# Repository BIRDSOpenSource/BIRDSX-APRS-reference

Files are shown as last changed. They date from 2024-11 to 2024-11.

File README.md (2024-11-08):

<div align="center">
  <a href="https://lean-sat.org/opensource/">
  
  </a>
</div> 

<div align="center">
  birds x
</div>

# BIRDSX-APRS-reference
 Documentation for the APRS Reference files of the BIRDSX Satellite.

## About the BIRDSX Program:

The Mission Statement of the Project is:

> “The goal of our project is to bring diversity to the space sector and democratize the usage of space.”

The project is led by Kyushu Institute of Technology in Japan and involves students from XXX,XXX and Japan.

Satellite Names: Dragonfly (Japan), 

Stakeholders:  Our stakeholders are Kyushu Institute of Technology (Kyutech) and the Association for Radio Digital Communications (ARDC).

Project duration: 2023-2024

CubeSat: 2U (20x10x10) cm3

Weight: 1.13kg

Launch Date: 21st February 2025

BIRDS-X project is a 2U CubeSat dedicated to amateur radio communication.

## Organisation structure

```bash

├── .gitattributes
├── BIRDS_Solar-panel-attachment-procedure_v2.2.pdf
├── Manual (SML-2K1MV1) (1).pdf
├── LICENSE
└── README.md

```

## Features

## I like this project, can I help you?
You are welcome 🙂

* Give us a star ⭐
* Watch repository to be notified about updates 👀
* If you will find some errors, report them in Issues 🐞
* Try Birds designs on some real computer and let us know how it worked in Discussions. 💬
* We would greatly appreciate if you would also tell others about this ecosystem, it helps us to improve BIRDS Open Source. Thank you!

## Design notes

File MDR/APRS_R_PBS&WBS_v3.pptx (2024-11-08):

## APRS Reference Board (APRS-R)

## Function and Performance

- Purpose : Provide satellite APRS digipeating for Amateur Radio Community.
- Function 1: Digipeater APRS packets from amateur radio stations on the ground.
Performance 1a: Transmit satellite APRS beacon to ground
Performance 1b: Receive and retransmit APRS packets from amateur radio stations.
Performance 1c: Transfer the received data packets to desired micro controller.

## Function and Performace

- Function 2 : Store the received data.
Performance 2a: Store the data to satellite’s specified memory location.
- Function 3 : Send data to the main ground stations.
Performance 3a: Transfer stored data to COMM MCU for download via UHF 4800 bps to ground stations.

## PBS

Satellite
1.1
Payload
1.1.2
APRS Reference
1.1.2.1
Transceiver
1.1.2.1.1
Terminal Node Controller (TNC)
1.1.2.1.2
Main Control Unit (MCU)
1.1.2.1.3
Memory
1.1.2.1.4
VHF Antenna
1.1.2.1.5

## WBS

Payload
1.1.2
APRS Reference
1.1.2.1
Transceiver
1.1.2.1.1
Terminal Node Controller (TNC)
1.1.2.1.2
Procurement
1.1.2.1.1.1
Assemble
1.1.2.1.1.2
Test
1.1.2.1.1.3
Procurement
1.1.2.1.2.1
Assemble
1.1.2.1.2.2
Test
1.1.2.1.2.3

## WBS (cont’l)

Payload
1.1.2
APRS Reference
1.1.2.1
Main Control Unit (MCU)
1.1.2.1.3
Memory
1.1.2.1.4
Procurement
1.1.2.1.3.1
Assemble
1.1.2.1.3.2
Test
1.1.2.1.3.3
Procurement
1.1.2.1.4.1
Assemble
1.1.2.1.4.2
Test
1.1.2.1.4.3

## WBS (cont’l)

Payload
1.1.2
APRS Reference
1.1.2.1
Main Control Unit (MCU)
1.1.2.1.3
Memory
1.1.2.1.4
Procurement
1.1.2.1.3.1
Assemble
1.1.2.1.3.2
Test
1.1.2.1.3.3
Procurement
1.1.2.1.4.1
Assemble
1.1.2.1.4.2
Test
1.1.2.1.4.3

## WBS (cont’l)

Payload
1.1.2
APRS Reference
1.1.2.1
VHF Antenna
1.1.2.1.5
Procurement
1.1.2.1.3.1
Assemble
1.1.2.1.3.2
Test
1.1.2.1.3.3

## Block Diagram

APRS Reference Payload

ARPS Reference MCU

VHF band

UART

TNC/APRS module

1200bps
AFSK

VHF FM Transceiver

Mission Boss

OBC

SPI

Flash Memory

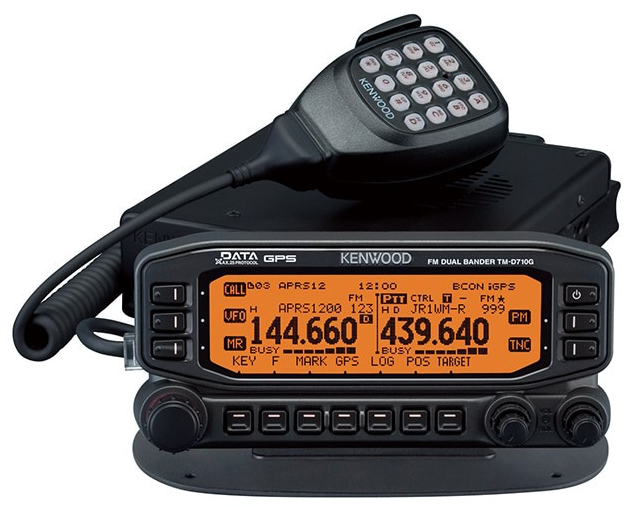
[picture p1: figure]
TM-D710G/TM-D710GS（生産完了品） | FMトランシーバー | アマチュア無線 | 無線通信 | KENWOOD

Amateur Radio Users or
Ground Terminal

UHF band

COMM MCU

COMM TRX

Ground station

9

## Link Budget

ELEVATION | | 10° | 20° | 30° | 40° | 50° | 60° | 70° | 80°
GROUND STATION
Transmit Output Power | [W] | 50 | 50 | 50 | 50 | 50 | 50 | 50 | 50
Transmit Output Power | [dBm] | 47 | 47 | 47 | 47 | 47 | 47 | 47 | 47
Antenna Gain | [dB] | 16 | 16 | 16 | 16 | 16 | 16 | 16 | 16
Transmission Line Loss | [dB] | 3.5 | 3.5 | 3.5 | 3.5 | 3.5 | 3.5 | 3.5 | 3.5
EIRP | [dBm] | 59.5 | 59.5 | 59.5 | 59.5 | 59.5 | 59.5 | 59.5 | 59.5
UPLINK PATH
GS Antenna Pointing Loss | [dB] | 3 | 3 | 3 | 3 | 3 | 3 | 3 | 3
Polarization Loss | [dB] | 3 | 3 | 3 | 3 | 3 | 3 | 3 | 3
Atmospheric + Ionospheric Losses | [dB] | 1.4 | 1.4 | 1.4 | 1.4 | 1.4 | 1.4 | 1.4 | 1.4
Path Loss | [dB] | 139.2 | 135.9 | 133.5 | 130.9 | 130.3 | 129.4 | 128.7 | 128.3
Antenna Pointing Loss | [dB] | 3 | 3 | 3 | 3 | 3 | 3 | 3 | 3
Effective Attenuation | [dB] | 137.1 | 133.8 | 131.4 | 128.8 | 128.2 | 127.3 | 126.6 | 126.2
Power at the satellite | [dBm] | -90.1 | -86.8 | -84.4 | -81.8 | -81.2 | -80.3 | -79.6 | -79.2
SATELLITE
Antenna Gain + Cable Loss | [dB] | 0.4 | 0.4 | 0.4 | 0.4 | 0.4 | 0.4 | 0.4 | 0.4
Transceiver Received Power | [dBm] | -89.7 | -86.4 | -84 | -81.4 | -80.8 | -79.9 | -79.2 | -78.8
Minimum Received Power | [dBm] | -85 | -85 | -85 | -85 | -85 | -85 | -85 | -85
Link Margin | [dB] | -4.7 | -1.4 | 1 | 3.6 | 4.2 | 5.1 | 5.8 | 6.2

## Link Budget

ELEVATION | | 10° | 20° | 30° | 40° | 50° | 60° | 70° | 80°
SATELLITE
Transmit Output Power | [W] | 0.48 | 0.48 | 0.48 | 0.48 | 0.48 | 0.48 | 0.48 | 0.48
Transmit Output Power | [dBm] | 27.8 | 27.8 | 27.8 | 27.8 | 27.8 | 27.8 | 27.8 | 27.8
Antenna Gain + Cable Loss | [dB] | 0.4 | 0.4 | 0.4 | 0.4 | 0.4 | 0.4 | 0.4 | 0.4
EIRP | [dBm] | 28.2 | 28.2 | 28.2 | 28.2 | 28.2 | 28.2 | 28.2 | 28.2
DOWNLINK PATH
Satellite Antenna Pointing Loss | [dB] | 3 | 3 | 3 | 3 | 3 | 3 | 3 | 3
Polarization Loss | [dB] | 3 | 3 | 3 | 3 | 3 | 3 | 3 | 3
Atmospheric + Ionospheric Losses | [dB] | 1.4 | 1.4 | 1.4 | 1.4 | 1.4 | 1.4 | 1.4 | 1.4
Path Loss | [dB] | 139.2 | 135.9 | 133.5 | 130.9 | 130.3 | 129.4 | 128.7 | 128.3
Antenna Pointing Loss | [dB] | 3 | 3 | 3 | 3 | 3 | 3 | 3 | 3
Effective Attenuation | [dB] | 149.2 | 145.9 | 143.5 | 140.9 | 140.3 | 139.4 | 138.7 | 138.3
Power at the ground station | [dBm] | -121.4 | -118.1 | -115.7 | -113.1 | -112.5 | -111.6 | -110.9 | -110.5
GROUND STATION
Antenna Gain | [dB] | 16 | 16 | 16 | 16 | 16 | 16 | 16 | 16
Transmission Line Loss | [dB] | 3.5 | 3.5 | 3.5 | 3.5 | 3.5 | 3.5 | 3.5 | 3.5
Transceiver Received Power | [dBm] | -108.9 | -105.6 | -103.2 | -100.6 | -100 | -99.1 | -98.4 | -98
Minimum Received Power | [dBm] | -110 | -110 | -110 | -110 | -110 | -110 | -110 | -110
Link Margin | [dB] | 1.1 | 4.4 | 6.8 | 9.4 | 10 | 10.9 | 11.6 | 12

## RAS

SR 1.1 – payload shall be controllable through an uplink command from a control ground station.
Design Requirements | Verification Requirements | Verification Method
Command will be sent from ground station using UHF uplink frequency | Measure receivable signal power of COMM transceiver | Using spectrum analyzer
OBC will relay the command to Mission Boss to activate APRS Reference payload | Check if the APRS/SF-WARD payload is activated/deactivated | Using terminal software to read APRS Reference MCU

## RAS

SR 1.2 – VHF transceiver operating in half-duplex will receive data from amateur radio users/ground terminal.
Design Requirements | Verification Requirements | Verification Method
Receiver will demodulate FM signal received | Check AFSK output of Receiver | Using spectrum analyzer
TNC will decode received AFSK signal | Check data output of TNC | Display Serial Output of TNC through Serial Monitor on PC
APRS Reference payload will receive transmitted data and store it. | Check received data if it matches transmitted data through wired testing | Display received OBC data through Serial on PC
| Check stored data in flash memory. | Read Flash Memory through APRS Reference Serial Interface

SR 1.2 – VHF transceiver operating in half-duplex will receive mission data from ground sensors.

## RAS

SR 1.3 – Payload shall store received packets (APRS message and ground sensor) into memory
Design Requirements | Verification Requirements | Verification Method
APRS Reference MCU shall process received AX.25 frame into correct fields | Check processed data of APRS Reference MCU | Display processed data through serial interface
Flash memory capacity of at least 32MB | Check specification and writable memory | Through write operations

SR 1.2 – VHF transceiver operating in half-duplex will receive mission data from ground sensors.

## RAS

SR 1.4 – Payload shall transmit stored data to ground station upon command from ground station using COM data downlink frequency
Design Requirements | Verification Requirements | Verification Method
COMM MCU shall read stored memory in APRS Reference Flash memory for downlink | Check data transmitted by COMM | Display received data

SR 1.2 – VHF transceiver operating in half-duplex will receive mission data from ground sensors.

## Schedule

TASK | 2022 | | | | 2023 | | | | | | | | | | | | | | | | | | | | | | | | | | | | | | | | | | | | | | | | | | | | | | | | 2024
| Dec | | | | Jan | | | | Feb | | | | Mar | | | | Apr | | | | May | | | | Jun | | | | Jul | | | | Aug | | | | Sep | | | | Oct | | | | Nov | | | | Dec | | | | Jan | | | | Feb
| 1 | 2 | 3 | 4 | 1 | 2 | 3 | 4 | 1 | 2 | 3 | 4 | 1 | 2 | 3 | 4 | 1 | 2 | 3 | 4 | 1 | 2 | 3 | 4 | 1 | 2 | 3 | 4 | 1 | 2 | 3 | 4 | 1 | 2 | 3 | 4 | 1 | 2 | 3 | 4 | 1 | 2 | 3 | 4 | 1 | 2 | 3 | 4 | 1 | 2 | 3 | 4 | 1 | 2 | 3 | 4 | 1 | 2 | 3 | 4
Check legacy missions' info
Procurement Components
Bread board model
Programming MCU
EM development
Integration with other satellite subsystems
Space Environment Test
FM development and final space environment tests

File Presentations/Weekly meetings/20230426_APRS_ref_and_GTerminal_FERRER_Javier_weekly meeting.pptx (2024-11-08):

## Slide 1

APRS Reference & Ground Terminal – Weekly meeting

FERRER, Javier

Date: 2023/04/26
Meeting: In-person meeting
Time: 02:40 PM – hh:mm JST

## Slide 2

Tasks performed during this week

- Checking S&F MCU board coding
- Ground Terminal
- BIRDS-X room

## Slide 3

- Checking S&F MCU board coding

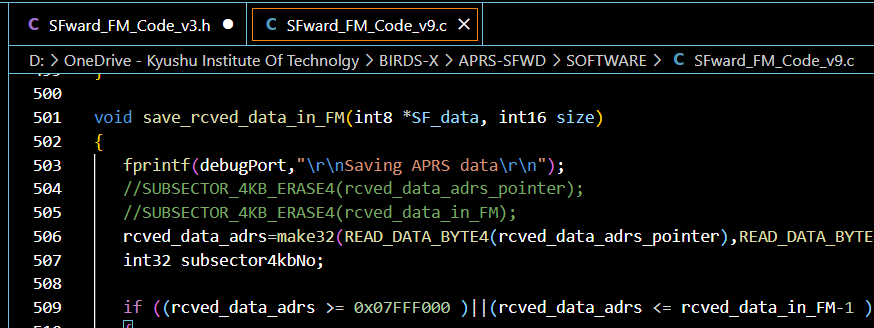
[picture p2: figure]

BIRDS-3
FAB

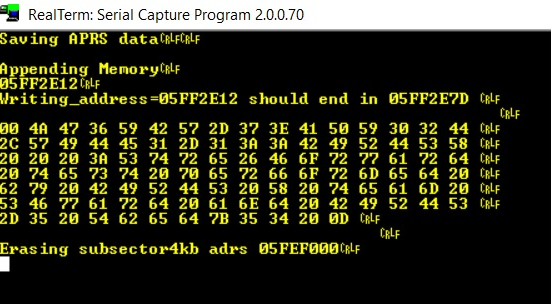
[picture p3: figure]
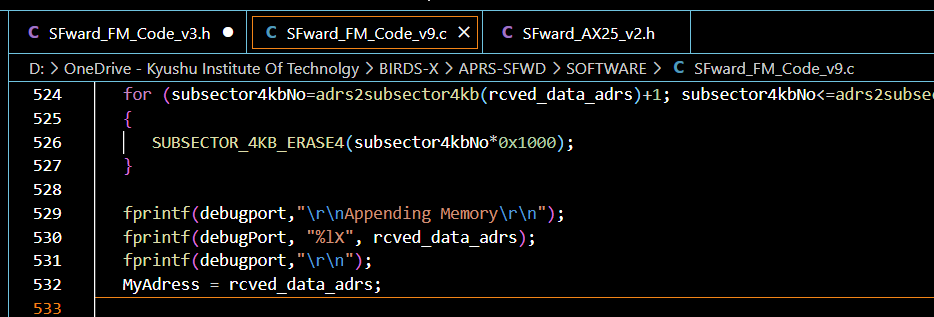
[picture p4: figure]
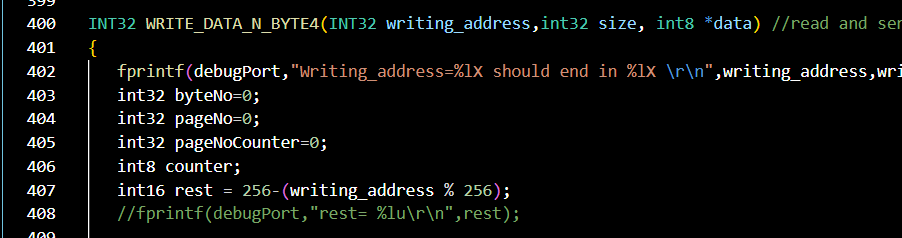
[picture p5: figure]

APRS- S&F board

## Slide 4

Ground Terminal

VHF Omnidirectional Antenna

Sensors

SPI

Transceiver

BIRDS-3
FAB

UART

MCU & TNC

Flash Memory

EPS

SPI

BIRDS-5
OBC

Block diagram MDR

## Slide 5

Ground Terminal

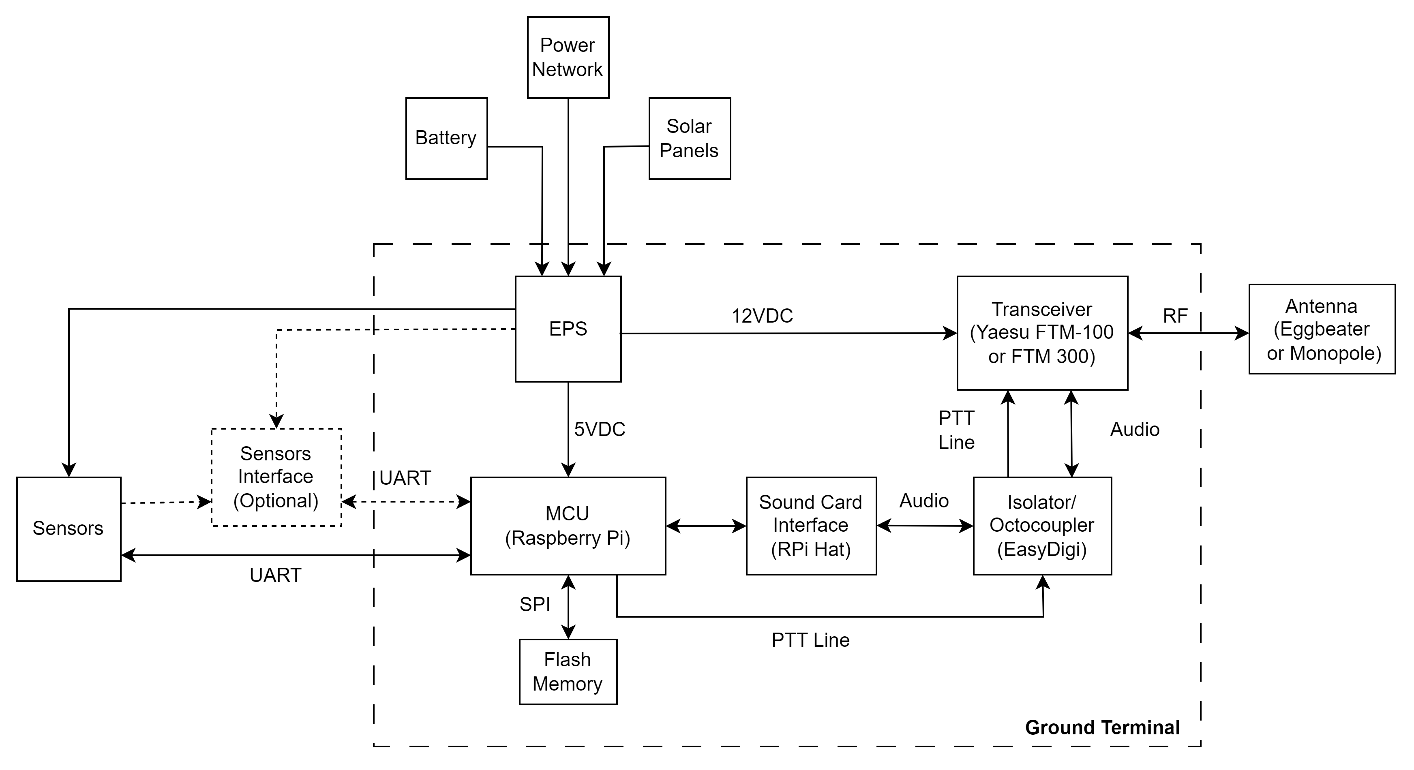
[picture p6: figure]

BIRDS-3
FAB

BIRDS-5
OBC

Block diagram - updated

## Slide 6

Hardware available for testing

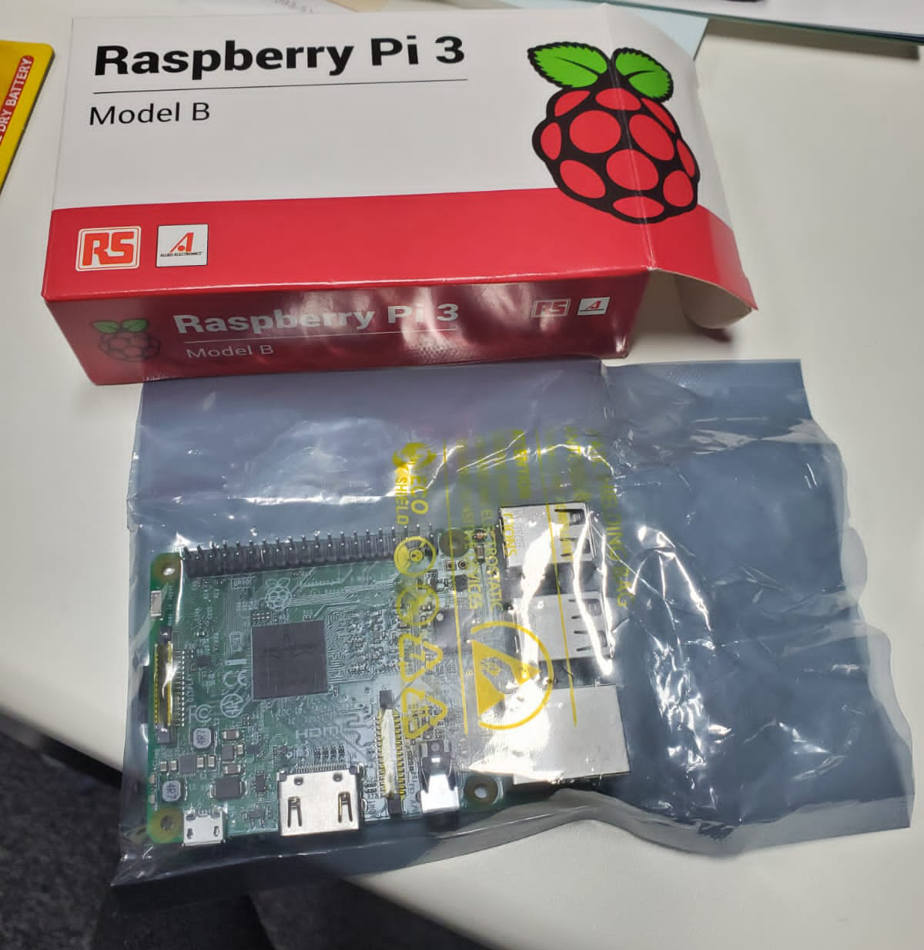
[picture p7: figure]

Raspberry Pi 3B

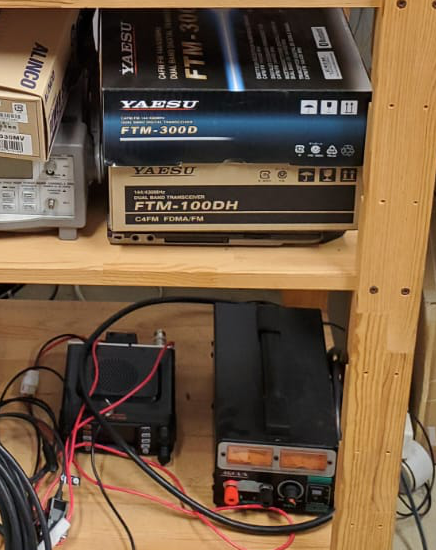
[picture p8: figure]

Transceivers
Yaesu FTM-100DH
Yaesu FTM-300D

BIRDS-3
FAB

BIRDS-5
OBC

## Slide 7

Next tasks

- Start coding the BIRDS-X S&F version adapted to commands coming from BIRDS-X Mission Boss
- Ground Terminal hardware components procurement.
- BIRDS-X room

BIRDS-3
FAB

BIRDS-5
OBC

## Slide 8

APRS Reference & Ground Terminal – Weekly meeting

FERRER, Javier

Date: 2023/04/19
Meeting: In-person meeting
Time: 02:40 PM – hh:mm JST

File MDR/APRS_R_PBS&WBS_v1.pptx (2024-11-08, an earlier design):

## APRS Reference Board

## PBS

APRS/R
Payload
1.1.2.3
APRS-DP
1.1.2.3.1
APRS Capable Radio
1.1.2.3.2
VHF Antenna
1.1.2.3.1.5
MCU
1.1.2.3.1.3
TNC
1.1.2.3.1.2
Transceiver
1.1.2.3.1.1
Memory
1.1.2.3.1.4

## WBS

APRS-DP
1.1.2.3.1
Memory
1.1.2.3.1.4
MCU
1.1.2.3.1.3
TNC
1.1.2.3.1.2
Transceiver
1.1.2.3.1.1
Procurement
1.1.2.3.1.1.1
Assemble
1.1.2.3.1.1.2
Test
1.1.2.3.1.1.3
Procurement
1.1.2.3.1.2.1
Assemble
1.1.2.3.1.2.2
Test
1.1.2.3.1.2.3
Procurement
1.1.2.3.1.3.1
Assemble
1.1.2.3.1.3.2
Test
1.1.2.3.1.3.3
Procurement
1.1.2.3.1.4.1
Assemble
1.1.2.3.1.4.2
Test
1.1.2.3.1.4.3
VHF Antenna
1.1.2.3.1.5
Procurement
1.1.2.3.1.5.1
Assemble
1.1.2.3.1.5.2
Test
1.1.2.3.1.5.3

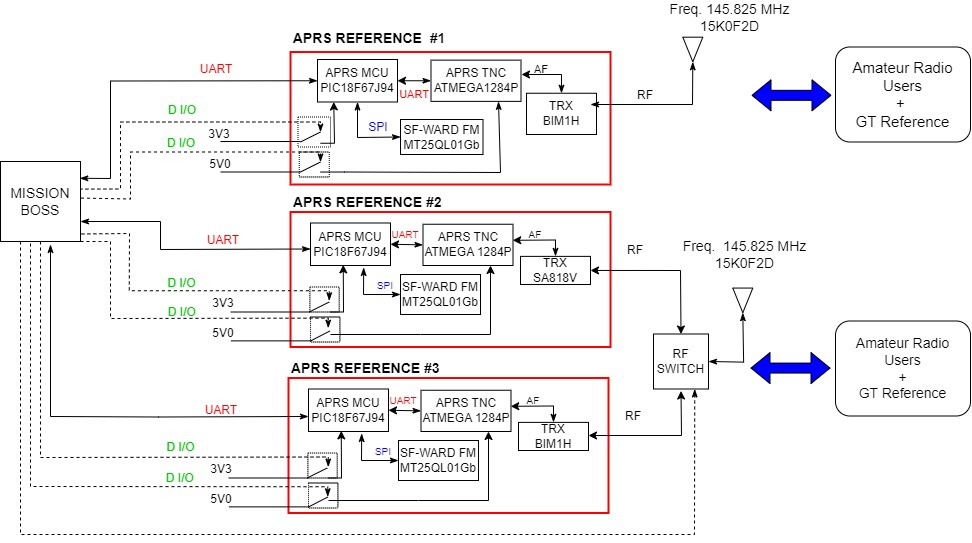
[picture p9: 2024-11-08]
APRS_FM_block_diagram.jpg

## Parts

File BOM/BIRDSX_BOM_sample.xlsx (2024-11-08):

Qty | Value | Description | Mass (g) | Manufacturer | Manufacturer Part Number | Price Unit (U$D) | Total Price (U$D)
1 |  | LED | 0.014 | OSRAM | LS Q976-NR-1 (https://www.mouser.com/ProductDetail/ams-OSRAM/LS-Q976-NR-1?qs=K5ta8V%252BWhtbwdFgXKu1Oiw%3D%3D) | 0.00 | 0.00
4 |  | LED | 0.00372 | Rohm | SML-E12V8WT86 | 0.00 | 0.00
1 |  | PIN HEADER |  |  |  | 0.00 | 0.00
1 |  | PIN HEADER | N/A | Hirose | A3B-50PA-2DS(51) | 32.16 | 32.16
1 | 0.025 | RESISTOR | N/A | Vishay Dale | WSL0805R0250FEA18 | 1.06 | 1.06
2 | 0.025 |  | N/A | Vishay Dale | WSL0805R0250FEA18 | 1.06 | 2.12
9 | 0.1u | CAPACITOR | N/A | Kemet | C0603C104K3RAC7867 | 1.06 | 9.58
4 | 0.1uF | CAPACITOR | N/A | Kemet | C0603C104K3RAC7867 | 1.06 | 4.26
1 | 0.1uF | CAPACITOR | N/A | Kemet | C0603C104K3RAC7867 | 1.06 | 1.06
2 | 100k | RESISTOR | N/A | YAGEO | RC0603FR-07100KL | 1.06 | 2.13
3 | 100uF | CAPACITOR | N/A | Samsung | CL21X107MRYN3WE | 10.64 | 31.92
13 | 10k | RESISTOR | N/A | YAGEO | RN73H1JTTD1002F50 | 3.25 | 42.29
1 | 10uF | CAPACITOR | N/A | TDK Corporation | C1608X7S0J106M080AC | 4.79 | 4.79
1 | 10uH | INDUCTOR | N/A | KEMET | L0805R100KPWST | 2.66 | 2.66
1 | 120k | RESISTOR | N/A | KOA Speer Electronics | RK73H1JTTD1203F | 1.06 | 1.06
1 | 15k | RESISTOR | N/A | KOA Speer Electronics, Inc. | RK73H1JTTD1502F | 1.06 | 1.06
4 | 18p | CAPACITOR | N/A | YAGEO | CC0805JRNPO0BN180 | 1.29 | 5.17
4 | 1k | RESISTOR | N/A | KOA Speer Electronics | RK73H1JTTD1001F | 1.06 | 4.26
3 | 1u | CAPACITOR | N/A | YAGEO | CC0201MRX5R5BB105 | 1.06 | 3.19
2 | 1uF | CAPACITOR | N/A | YAGEO | CC0201MRX5R5BB105 | 1.06 | 2.13
2 | 2.2k | RESISTOR | N/A | KOA Speer Electronics | RK73H1JTTD2201F | 1.06 | 2.13
1 | 2.2n | CAPACITOR | N/A | KEMET | C0603C222K1HACAUTO | 1.29 | 1.29
2 | 200k | RESISTOR | N/A | KOA Speer Electronics, Inc. | RK73H1JTTD2203F | 1.06 | 2.13
1 | 20MHZ | CRYSTAL | N/A | QANTEK | QCS20.0000F18B23R | 5.14 | 5.14
3 | 220k | RESISTOR | N/A | KOA Speer Electronics, Inc. | RK73B2ATTD204J | 1.06 | 3.19
1 | 3.3k | RESISTOR | N/A | KOA Speer Electronics | RK73H1JTTD3301F | 1.06 | 1.06
2 | 330 | RESISTOR | N/A | Panasonic | ERJ-U03F3300V | 1.60 | 3.19
1 | 4.3k | RESISTOR | N/A | KOA Speer Electronics | RK73B1JTTD432J | 1.06 | 1.06
1 | 47k | RESISTOR | N/A | KOA Speer Electronics, Inc. | RK73B2ATTD473J | 0.00 | 0.00
1 | 5.1k | RESISTOR | N/A | KOA Speer Electronics | RK73H1JTTD5101F | 1.06 | 1.06
1 | 74LVC1G125GW | Bus buffer/line driver; 3-state | N/A | Nexperia | 74LVC1G125GW,125 | 4.03 | 4.03
1 | 8MHZ | CRYSTAL | N/A | Fox Electronics | FC4SDCBMF8.0‐T1 | 17.56 | 17.56
1 | ATMEGA644-20PU | 8-bit Microcontroller with 64K Bytes In-System Programmable Flash | 6 | Microchip Technology | ATMEGA644-20PU | 81.47 | 81.47
1 | BIM1H | Transceiver | N/A | Radiometrix |  | 876.28 | 876.28
3 | BIRDS5_LTC4361 |  |  |  |  | 0.00 | 0.00
4 | DTC144EKA |  | N/A | Micro Commercial Co | DTC144EKA ---DTC144EKAT146 | 2.81 | 11.25
1 | MCP602SN | Single Op Amp 2.7V to 6.0V Single Supply CMOS | N/A | Microchip Technology | MCP602-E/SN | 9.65 | 9.65
1 | MMCX_908_222101T |  | N/A | Amphenol | 908-22101-TC | 91.28 | 91.28
1 | MT25QL01GBBB8ESF-0SIT | IC FLASH 1GBIT 108MHZ 16SOIC | N/A | Micron | MT25QL01GBBB8ESF-0SIT | 143.84 | 143.84
1 | PIC18F67J94-I_PT | MCU 8-Bit 128K Flash LCD USB XLP TQFP64 Microchip PIC18F67J94-I/PT, 8bit PIC Microcontroller, 64MHz, 128 kB Flash, 64-Pin TQFP | N/A | Microchip | PIC18F67J94-I/PT | 62.93 | 62.93
1 | PVG3A200C01R00 | Res Cermet Trimmer 20 Ohm 20% 1/4W 1(Elec)/1(Mech)Turn 2.2mm (3.6 X 3.6 X 2mm) J-Hook SMD T/R | N/A | Bourns Inc. | PVG3A203C01R00 | 15.73 | 15.73
1 | RAB_ACCESS |  |  |  |  | 0.00 | 0.00
3 | SQ1922EEH | MOSFET 2N-CH 20V SC70-6 | N/A | Vishay Siliconix | SQ1922EEH | 5.40 | 16.19
 |  |  |  |  | TOTAL (U$D) |  | 1501.35
 |  |  |  |  | Board Not Included

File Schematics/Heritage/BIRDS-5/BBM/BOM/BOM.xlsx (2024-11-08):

Column1
Partlist exported from C:/Users/MUJUNI/Desktop/Shematics V2/Schematic SF 1_12_2020 8 semi3.sch at 12/13/2020 2:30 PM
APD1 LEDSML0603 SML0603 LED
APD2 LEDSML0603 SML0603 LED
APD3 LEDSML0603 SML0603 LED
APD4 LEDSML0603 SML0603 LED
BAL MABA-010245-BALUN MABA-010245-BALUN MABA-010245-BALUN
C1 0.1uF CC0603 C0603 CAPACITOR, European symbol NONE C
C2 0.1uF CC0603 C0603 CAPACITOR, European symbol NONE C
C3 0.1u CC0603 C0603 CAPACITOR, European symbol NONE C
C4 1u CC0603 C0603 CAPACITOR, European symbol NONE C
C5 0.1u CC0603 C0603 CAPACITOR, European symbol NONE C
C13 1uF CC0603 C0603 CAPACITOR, European symbol NONE C
C14 18pF CC0603 C0603 CAPACITOR, European symbol NONE C
C15 18pF CC0603 C0603 CAPACITOR, European symbol NONE C
C16 C-EUC0805 C0805 CAPACITOR, European symbol C
C17 0.1uF CC0603 C0603 CAPACITOR, European symbol NONE C
C18 10uF C-EUC0603 C0603 CAPACITOR, European symbol C
C19 C-EUC0805 C0805 CAPACITOR, European symbol C
C20 0.1uF CC0603 C0603 CAPACITOR, European symbol NONE C
C21 0.1uF C-EUC0603 C0603 CAPACITOR, European symbol C
C22 0.1uF C-EUC0603 C0603 CAPACITOR, European symbol C
C23 1uF C-EUC0603 C0603 CAPACITOR, European symbol C
C24 0.1uF C-EUC0603 C0603 CAPACITOR, European symbol C
C25 0.1uF C-EUC0603 C0603 CAPACITOR, European symbol C
C26 1uF C-EUC0603 C0603 CAPACITOR, European symbol C
C27 100uF C0805(2012) C0805
C28 10pF CC0603 C0603 CAPACITOR, European symbol NONE C
C29 6.8pF CC0603 C0603 CAPACITOR, European symbol NONE C
C30 18pF CC0603 C0603 CAPACITOR, European symbol NONE C
C31 18pF CC0603 C0603 CAPACITOR, European symbol NONE C
C35 100uF C0805(2012) C0805
C36 0.1u CC0603 C0603 CAPACITOR, European symbol NONE C
C37 1u CC0603 C0603 CAPACITOR, European symbol NONE C
C38 0.1u CC0603 C0603 CAPACITOR, European symbol NONE C
C39 1u CC0603 C0603 CAPACITOR, European symbol NONE C
C40 0.1u CC0603 C0603 CAPACITOR, European symbol NONE C
C41 0.1u CC0603 C0603 CAPACITOR, European symbol NONE C
C42 0.1u CC0603 C0603 CAPACITOR, European symbol NONE C
C43 0.1u CC0603 C0603 CAPACITOR, European symbol NONE C
C44 0.1u CC0603 C0603 CAPACITOR, European symbol NONE C
C45 2.2n CC0603 C0603 CAPACITOR, European symbol NONE C
FM_SF MT25QL01GBBB8ESF-0SIT MT25QL01GBBB8ESF-0SIT SOIC127P1032X265-16N IC FLASH 1GBIT 108MHZ 16SOIC IC FLASH 1GBIT 108MHZ 16SOIC 2.65mm Micron MT25QL01GBBB8ESF-0SIT RS
IC2 ATMEGA644-20PU ATMEGA644-20PU DIL40 8-bit Microcontroller with 64K Bytes In-System Programmable Flash ATMEGA644-20PU 1288340 23M5060 0
JP1 RAB_ACCESS RAB_ACCESS RAB_ACCESS
JP2 PINHD-2X25_2.00 2X25M PIN HEADER
JP3 JP1E JP1 JUMPER 61
JP4 JP1E JP1 JUMPER 61
L1 L-USL2012C L2012C INDUCTOR, American symbol L
L2 L-USL2012C L2012C INDUCTOR, American symbol L
L3 22nH L-USL2012C L2012C INDUCTOR, American symbol L
L5 10uH L-USL2012C L2012C INDUCTOR, American symbol L
MCU_SF PIC18F67J94-I_PT PIC18F67J94-I_PT QFP50P1200X1200X120-64N MCU 8-Bit 128K Flash LCD USB XLP TQFP64 Microchip PIC18F67J94-I/PT, 8bit PIC Microcontroller, 64MHz, 128 kB Flash, 64-Pin TQFP 70470236 https://www.alliedelec.com/microchip-technology-inc-pic18f67j94-i-pt/70470236/ MCU 8-Bit 128K Flash LCD USB XLP TQFP64 Microchip PIC18F67J94-I/PT, 8bit PIC Microcontroller, 64MHz, 128 kB Flash, 64-Pin TQFP 1.2mm Microchip PIC18F67J94-I/PT 579-PIC18F67J94-I/PT https://www.mouser.com/Search/Refine.aspx?Keyword=579-PIC18F67J94-I%2FPT 1652172 http://uk.rs-online.com/web/p/products/1652172
MOS1 SQ1922EEH SQ1922EEH SOT65P210X110-6N
MOS2 SQ1922EEH SQ1922EEH SOT65P210X110-6N
OCP1 LTC4361-2 LTC4361-2 DFN
OCP2 LTC4361-2 LTC4361-2 DFN
OPAMP MCP602SN MCP602SN SO08 Single Op Amp 2.7V to 6.0V Single Supply CMOS
OPAMP1 MCP602SN MCP602SN SO08 Single Op Amp 2.7V to 6.0V Single Supply CMOS
Q1 DTC144EKA DTC144EKA SOT346-R
Q2 DTC144EKA DTC144EKA SOT346-R
Q3 DTC144EKA DTC144EKA SOT346-R
R1 100k R-US_R0603 R0603 RESISTOR, American symbol R
R2 100k R-US_R0603 R0603 RESISTOR, American symbol R
R3 10k R-US_R0603 R0603 RESISTOR, American symbol R
R4 10k R-US_R0603 R0603 RESISTOR, American symbol R
R5 10k R-US_R0603 R0603 RESISTOR, American symbol R
R6 3.3k R-US_R0603 R0603 RESISTOR, American symbol R
R7 3.3k R-US_R0603 R0603 RESISTOR, American symbol R
R8 10k R-US_R0603 R0603 RESISTOR, American symbol R
R9 10k R-US_R0603 R0603 RESISTOR, American symbol R
R10 0.025 R0805(2012) R0805
R11 10k R-US_R0603 R0603 RESISTOR, American symbol R
R12 10k R-US_R0603 R0603 RESISTOR, American symbol R
R13 10k R-US_R0603 R0603 RESISTOR, American symbol R
R14 10k R-US_R0603 R0603 RESISTOR, American symbol R
R17 10k R-US_R0603 R0603 RESISTOR, American symbol R
R18 0.025 R-US_R0805 R0805 RESISTOR, American symbol R
R19 2.2k R-US_R0603 R0603 RESISTOR, American symbol R
R20 10k R-US_R0603 R0603 RESISTOR, American symbol R
R21 1k R-US_R0603 R0603 RESISTOR, American symbol R
R22 1k R-US_R0603 R0603 RESISTOR, American symbol R
R23 1k R-US_R0603 R0603 RESISTOR, American symbol R
R24 10k R-US_R0603 R0603 RESISTOR, American symbol R
R25 200k R-US_R0603 R0603 RESISTOR, American symbol R
R26 220k R-US_R0603 R0603 RESISTOR, American symbol R
R27 330 R-US_R0603 R0603 RESISTOR, American symbol R
R28 330 R-US_R0603 R0603 RESISTOR, American symbol R
R29 220k R-US_R0603 R0603 RESISTOR, American symbol R
R30 200k R-US_R0603 R0603 RESISTOR, American symbol R
R31 220k R-US_R0603 R0603 RESISTOR, American symbol R
R32 PVG3A200C01R00 PVG3A200C01R00 TRIM_PVG3A200C01R00 Res Cermet Trimmer 20 Ohm 20% 1/4W 1(Elec)/1(Mech)Turn 2.2mm (3.6 X 3.6 X 2mm) J-Hook SMD T/R Trimmer 20 Ohm 0.25w Smd 490-2647-1-ND https://www.digikey.jp/product-detail/en/bourns-inc/PVG3A200C01R00/490-2647-1-ND/666223 Bourns PVG3A200C01R00 TO-221 Bourns
R33 15k R-US_R0603 R0603 RESISTOR, American symbol R
R34 47k R-US_R0603 R0603 RESISTOR, American symbol R
R35 120k R-US_R0603 R0603 RESISTOR, American symbol R
R36 1k R-US_R0603 R0603 RESISTOR, American symbol R
R37 5.1k R-US_R0603 R0603 RESISTOR, American symbol R
R38 2.2k R-US_R0603 R0603 RESISTOR, American symbol R
R39 4.3k R-US_R0603 R0603 RESISTOR, American symbol R
RFCON MMCX_908_222101T MMCX_908_222101T MMCX_908_222101T
SFD1 LEDCHIPLED_0603 CHIPLED_0603 LED
SFD2 LEDCHIPLED_0603 CHIPLED_0603 LED
TCXO FOX924B FOX924B FOX924B
TRX1 BIM1H BIM1H BIM1H
TRX2 AX5243 AX5243 AX5243
U1 74LVC1G125GW 74LVC1G125GW SOT353-1 Bus buffer/line driver; 3-state
U2 74LVC1G125GW 74LVC1G125GW SOT353-1 Bus buffer/line driver; 3-state
XTAL_AP ECS-200-18-30BQ-DS ECS-200-18-30BQ-DS XTAL_ECS-200-18-30BQ-DS The ECX-53BQ is a miniature SMD Crystal with a 3.2 x 5 mm Crystal 20.0000mhz 18pf Smd XC1997CT-ND https://www.digikey.jp/product-detail/en/ecs-inc/ECS-200-18-30BQ-DS/XC1997CT-ND/4073672 ECS Inc. ECS-200-18-30BQ-DS SMD-4 ECS International
XTAL_SF ECS-80-18-20BQ-DS ECS-80-18-20BQ-DS XTAL_ECS-80-18-20BQ-DS compact SMD Crystal 8.0000MHZ 18PF SMD, CSM-8Q, 100ppm, 30ppm, 18pF Crystal XC2015CT-ND https://www.digikey.jp/product-detail/en/ecs-inc/ECS-80-18-20BQ-DS/XC2015CT-ND/4073726 ECS Inc. ECS-80-18-20BQ-DS SMD-4 ECS International

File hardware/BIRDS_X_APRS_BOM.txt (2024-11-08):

Part     Value                 Device                Package                 Description                                                                                                                    3D_PACKAGE ALLIED_NUMBER ALLIED_PRICE-STOCK                                                             AVAILABILITY CHECK_PRICES                                                                     DESCRIPTION                                                                                                                    DIGI-KEY_PART_NUMBER DIGI-KEY_PURCHASE_URL                                                                                                                                HEIGHT MANUFACTURER_NAME MANUFACTURER_PART_NUMBER MF                 MOUSER_PART_NUMBER   MOUSER_PRICE-STOCK                                                       MP             MPN OC_FARNELL OC_NEWARK OTHER_PART_NUMBER PACKAGE                    POPULARITY PRICE PURCHASE-URL                                                    RS_PART_NUMBER RS_PRICE-STOCK                                 SNAPEDA_LINK                                                                      SUPPLIER_NAME
APD1                           LEDSML0603            SML0603                 LED                                                                                                                                                                                                                                                                                                                                                                                                                                                                                                                                                                                                                                                                                                                                                                                                                                                                                                   17                                                                                                                                                                                                                                            
APD2                           LEDSML0603            SML0603                 LED                                                                                                                                                                                                                                                                                                                                                                                                                                                                                                                                                                                                                                                                                                                                                                                                                                                                                                   17                                                                                                                                                                                                                                            
APD3                           LEDSML0603            SML0603                 LED                                                                                                                                                                                                                                                                                                                                                                                                                                                                                                                                                                                                                                                                                                                                                                                                                                                                                                   17                                                                                                                                                                                                                                            
APD4                           LEDSML0603            SML0603                 LED                                                                                                                                                                                                                                                                                                                                                                                                                                                                                                                                                                                                                                                                                                                                                                                                                                                                                                   17                                                                                                                                                                                                                                            
C1       0.1uF                 CAPACITOR             M(1005)_US(0402)                                                                                                                                                                                                                                                                                                                                                                                                                                                                                                                                                                                                                                                                                                                                                                                                                                                                                                                                                                                                                                                                                                                                                            
C2       100uF                 CAPACITOR2012         M(2012)_US(0805)                                                                                                                                                                                                                                                                                                                                                                                                                                                                                                                                                                                                                                                                                                                                                                                                                                                                                                                                                                                                                                                                                                                                                            
C3       100uF                 CAPACITOR2012         M(2012)_US(0805)                                                                                                                                                                                                                                                                                                                                                                                                                                                                                                                                                                                                                                                                                                                                                                                                                                                                                                                                                                                                                                                                                                                                                            
C4       18pF                  CAPACITOR             M(1005)_US(0402)                                                                                                                                                                                                                                                                                                                                                                                                                                                                                                                                                                                                                                                                                                                                                                                                                                                                                                                                                                                                                                                                                                                                                            
C5       18pF                  CAPACITOR             M(1005)_US(0402)                                                                                                                                                                                                                                                                                                                                                                                                                                                                                                                                                                                                                                                                                                                                                                                                                                                                                                                                                                                                                                                                                                                                                            
C6       0.1uF                 CAPACITOR             M(1005)_US(0402)                                                                                                                                                                                                                                                                                                                                                                                                                                                                                                                                                                                                                                                                                                                                                                                                                                                                                                                                                                                                                                                                                                                                                            
C7       10uF                  CAPACITOR1608         M(1608)_US(0603)                                                                                                                                                                                                                                                                                                                                                                                                                                                                                                                                                                                                                                                                                                                                                                                                                                                                                                                                                                                                                                                                                                                                                            
C8       0.1uF                 CAPACITOR             M(1005)_US(0402)                                                                                                                                                                                                                                                                                                                                                                                                                                                                                                                                                                                                                                                                                                                                                                                                                                                                                                                                                                                                                                                                                                                                                            
C9       0.1uF                 CAPACITOR             M(1005)_US(0402)                                                                                                                                                                                                                                                                                                                                                                                                                                                                                                                                                                                                                                                                                                                                                                                                                                                                                                                                                                                                                                                                                                                                                            
C10      0.1uF                 CAPACITOR             M(1005)_US(0402)                                                                                                                                                                                                                                                                                                                                                                                                                                                                                                                                                                                                                                                                                                                                                                                                                                                                                                                                                                                                                                                                                                                                                            
C11      0.1uF                 CAPACITOR             M(1005)_US(0402)                                                                                                                                                                                                                                                                                                                                                                                                                                                                                                                                                                                                                                                                                                                                                                                                                                                                                                                                                                                                                                                                                                                                                            
C12      0.1uF                 CAPACITOR             M(1005)_US(0402)                                                                                                                                                                                                                                                                                                                                                                                                                                                                                                                                                                                                                                                                                                                                                                                                                                                                                                                                                                                                                                                                                                                                                            
C13      20pF                  CAPACITOR1608         M(1608)_US(0603)                                                                                                                                                                                                                                                                                                                                                                                                                                                                                                                                                                                                                                                                                                                                                                                                                                                                                                                                                                                                                                                                                                                                                            
C14      20pF                  CAPACITOR1608         M(1608)_US(0603)                                                                                                                                                                                                                                                                                                                                                                                                                                                                                                                                                                                                                                                                                                                                                                                                                                                                                                                                                                                                                                                                                                                                                            
C15      36pF                  CAPACITOR1608         M(1608)_US(0603)                                                                                                                                                                                                                                                                                                                                                                                                                                                                                                                                                                                                                                                                                                                                                                                                                                                                                                                                                                                                                                                                                                                                                            
C16      36pF                  CAPACITOR1608         M(1608)_US(0603)                                                                                                                                                                                                                                                                                                                                                                                                                                                                                                                                                                                                                                                                                                                                                                                                                                                                                                                                                                                                                                                                                                                                                            
C17      0.1uF                 CAPACITOR             M(1005)_US(0402)                                                                                                                                                                                                                                                                                                                                                                                                                                                                                                                                                                                                                                                                                                                                                                                                                                                                                                                                                                                                                                                                                                                                                            
C18      0.1uF                 CAPACITOR             M(1005)_US(0402)                                                                                                                                                                                                                                                                                                                                                                                                                                                                                                                                                                                                                                                                                                                                                                                                                                                                                                                                                                                                                                                                                                                                                            
C19      1uF                   CAPACITOR             M(1005)_US(0402)                                                                                                                                                                                                                                                                                                                                                                                                                                                                                                                                                                                                                                                                                                                                                                                                                                                                                                                                                                                                                                                                                                                                                            
C20      0.1uF                 CAPACITOR             M(1005)_US(0402)
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

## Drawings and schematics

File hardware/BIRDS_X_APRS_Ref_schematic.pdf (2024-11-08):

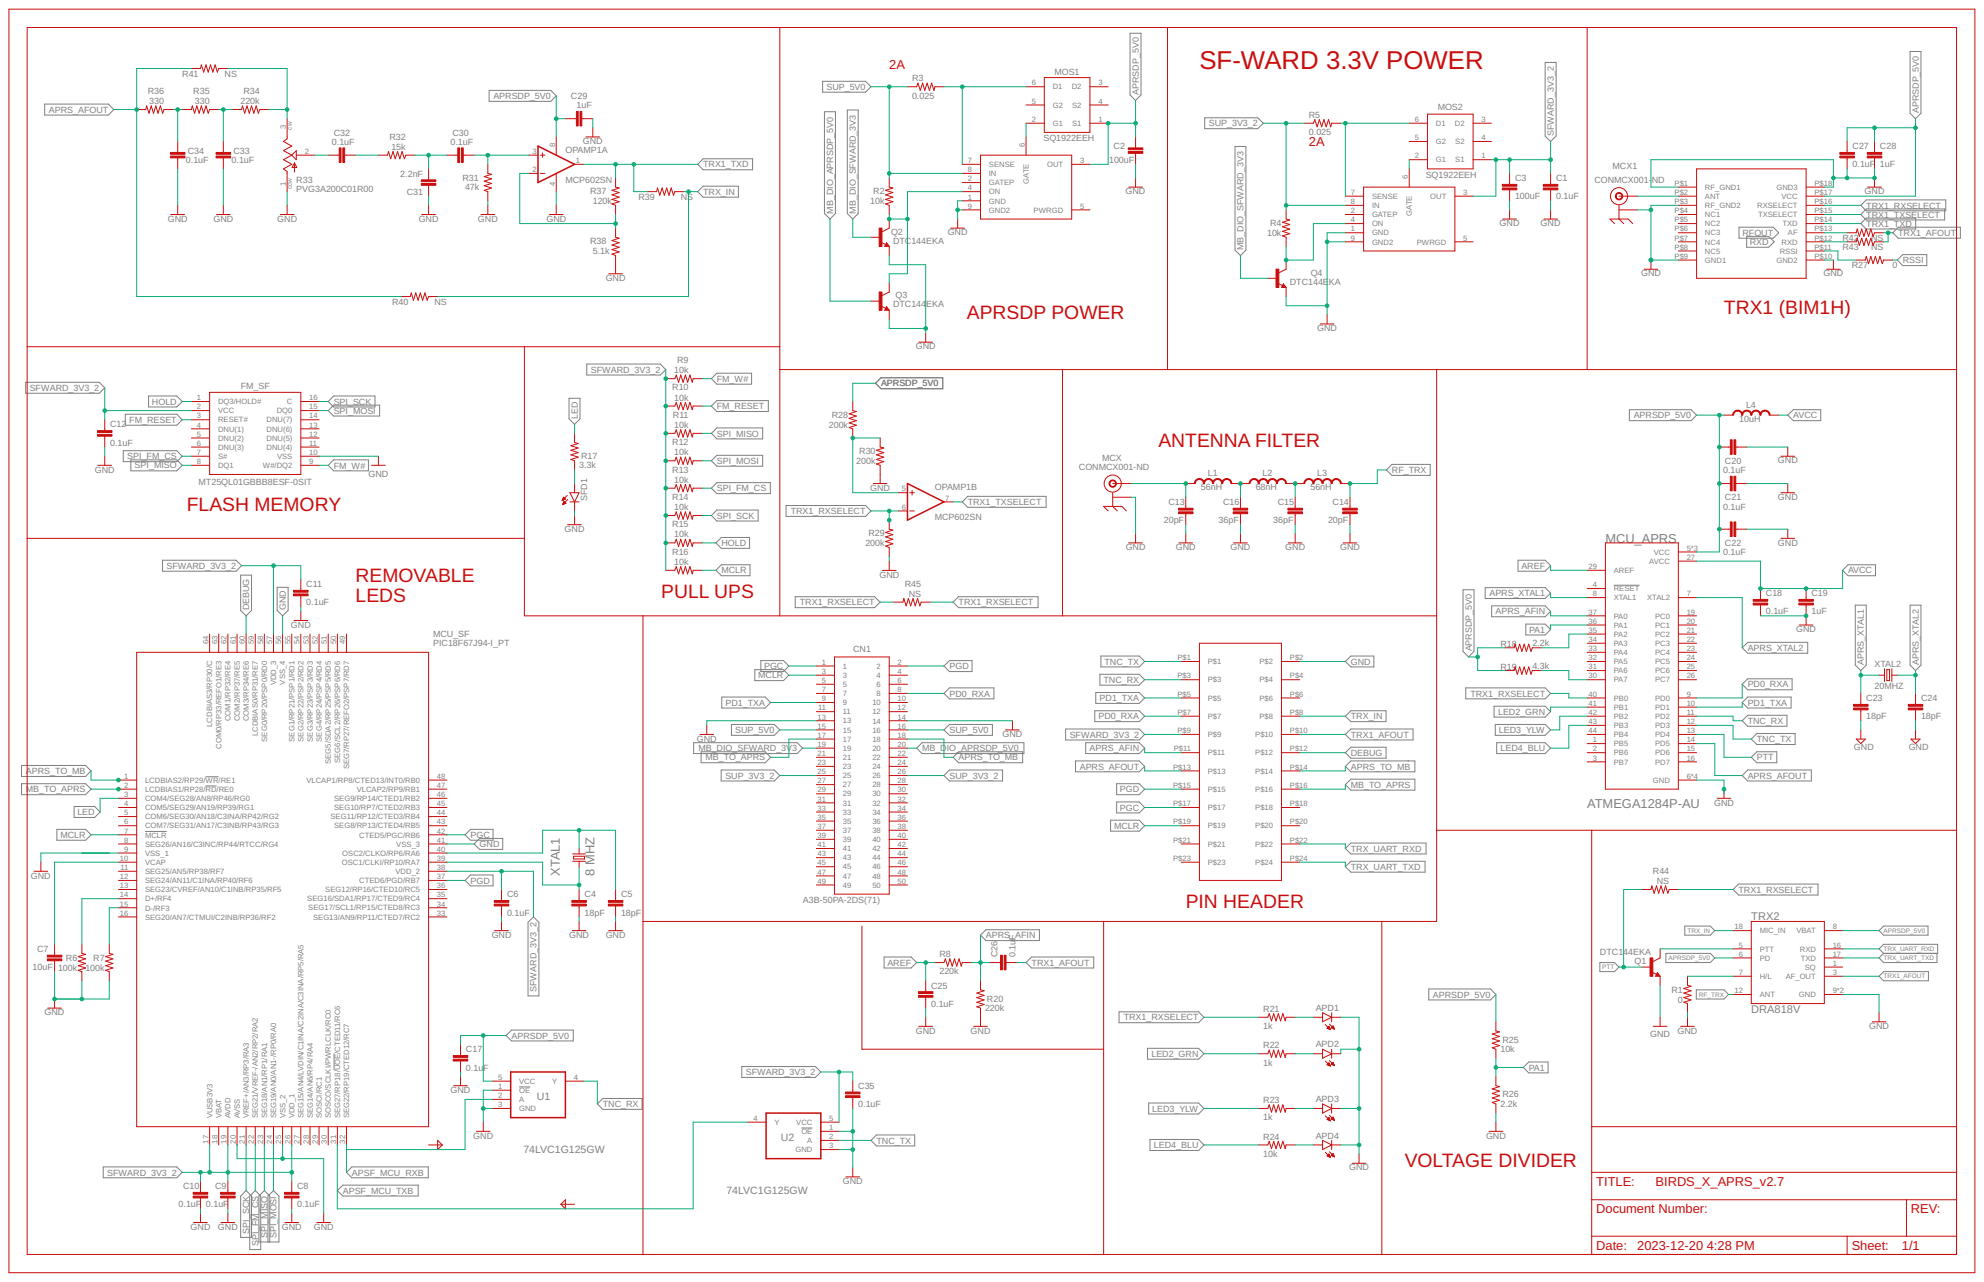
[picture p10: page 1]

ANTENNA FILTER | L4

SPI_FM_CS | 10 W#/DQ2

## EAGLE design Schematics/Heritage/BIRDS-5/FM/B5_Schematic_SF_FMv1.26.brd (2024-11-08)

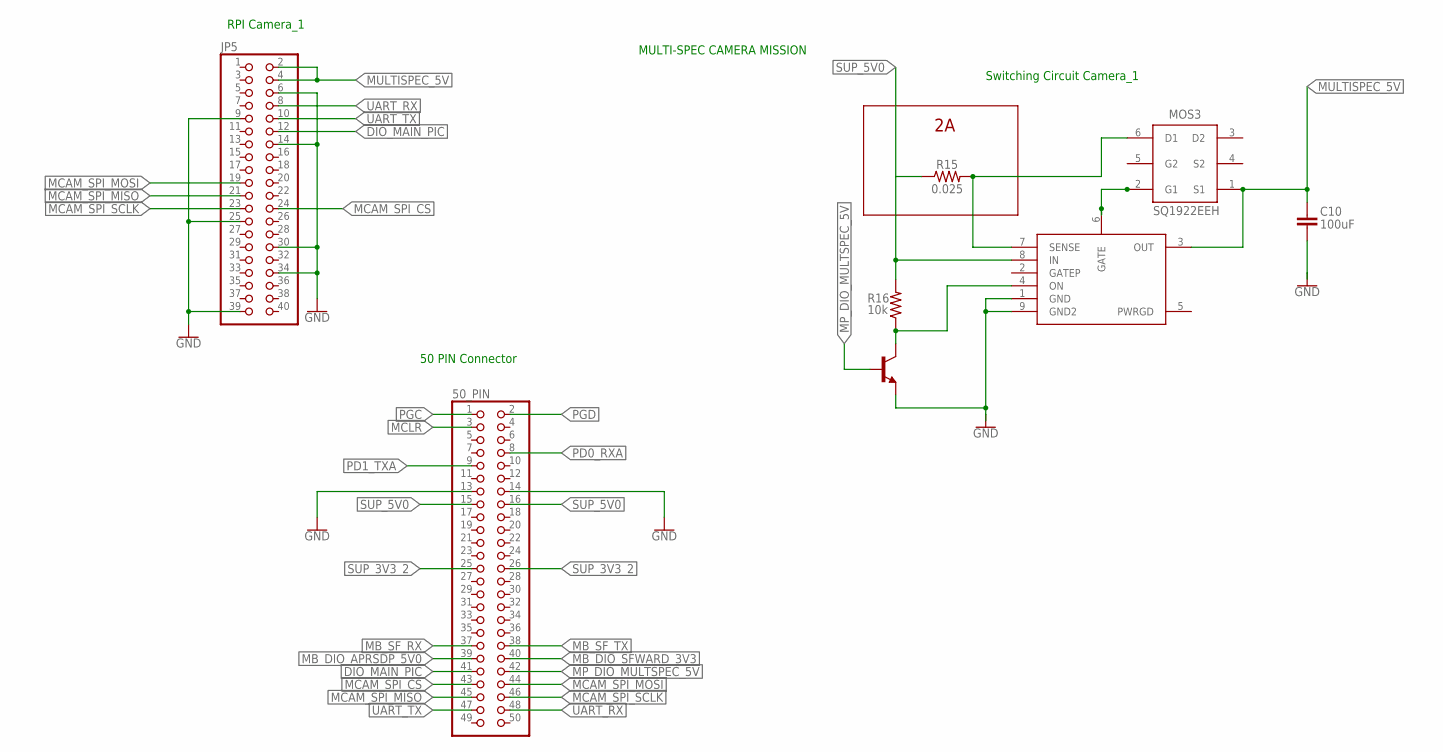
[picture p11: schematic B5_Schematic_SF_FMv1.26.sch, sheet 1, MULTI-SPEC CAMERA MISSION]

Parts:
50_PIN: PINHD-2X25_2.00; 2X25M
C10: 100uF; C0805
JP5: PINHD-2X20; 2X20
MOS3: SQ1922EEH; SOT65P210X110-6N
Q4: DTC144EKA; SOT346-R
R15: 0.025; R0805
R16: 10k; R0603
U$2: BIRDS5_LTC4361

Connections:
DIO_MAIN_PIC: 50_PIN.41, JP5.12
GATE1: MOS3.2 (G1), U$2.6 (GATE)
GND: 50_PIN.13, 50_PIN.14, C10.2, JP5.6, JP5.9, JP5.14, JP5.25, JP5.30, JP5.34, JP5.39, Q4.1 (E), U$2.1 (GND), U$2.9 (GND2); also elsewhere on the board
MB_DIO_APRSDP_5V0: 50_PIN.39; also elsewhere on the board
MB_DIO_SFWARD_3V3: 50_PIN.40; also elsewhere on the board
MB_SF_RX: 50_PIN.37; also elsewhere on the board
MB_SF_TX: 50_PIN.38; also elsewhere on the board
MCAM_SPI_CS: 50_PIN.43, JP5.24
MCAM_SPI_MISO: 50_PIN.45, JP5.21
MCAM_SPI_MOSI: 50_PIN.44, JP5.19
MCAM_SPI_SCLK: 50_PIN.46, JP5.23
MCLR: 50_PIN.3; also elsewhere on the board
MP_DIO_MULTSPEC_5V: 50_PIN.42, Q4.2 (B)
MULTISPEC_5V: C10.1, JP5.2, JP5.4, MOS3.1 (S1), U$2.3 (OUT)
ON1: Q4.3 (C), R16.1, U$2.4 (ON)
PD0_RXA: 50_PIN.8; also elsewhere on the board
PD1_TXA: 50_PIN.9; also elsewhere on the board
PGC: 50_PIN.1; also elsewhere on the board
PGD: 50_PIN.2; also elsewhere on the board
SENSE1: MOS3.6 (D1), R15.2, U$2.7 (SENSE)
SUP_3V3_2: 50_PIN.25, 50_PIN.26; also elsewhere on the board
SUP_5V0: 50_PIN.15, 50_PIN.16, R15.1, R16.2, U$2.8 (IN); also elsewhere on the board
UART_RX: 50_PIN.48, JP5.8
UART_TX: 50_PIN.47, JP5.10

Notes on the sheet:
RPI Camera_1
50 PIN Connector
Switching Circuit Camera_1
MULTI-SPEC CAMERA MISSION

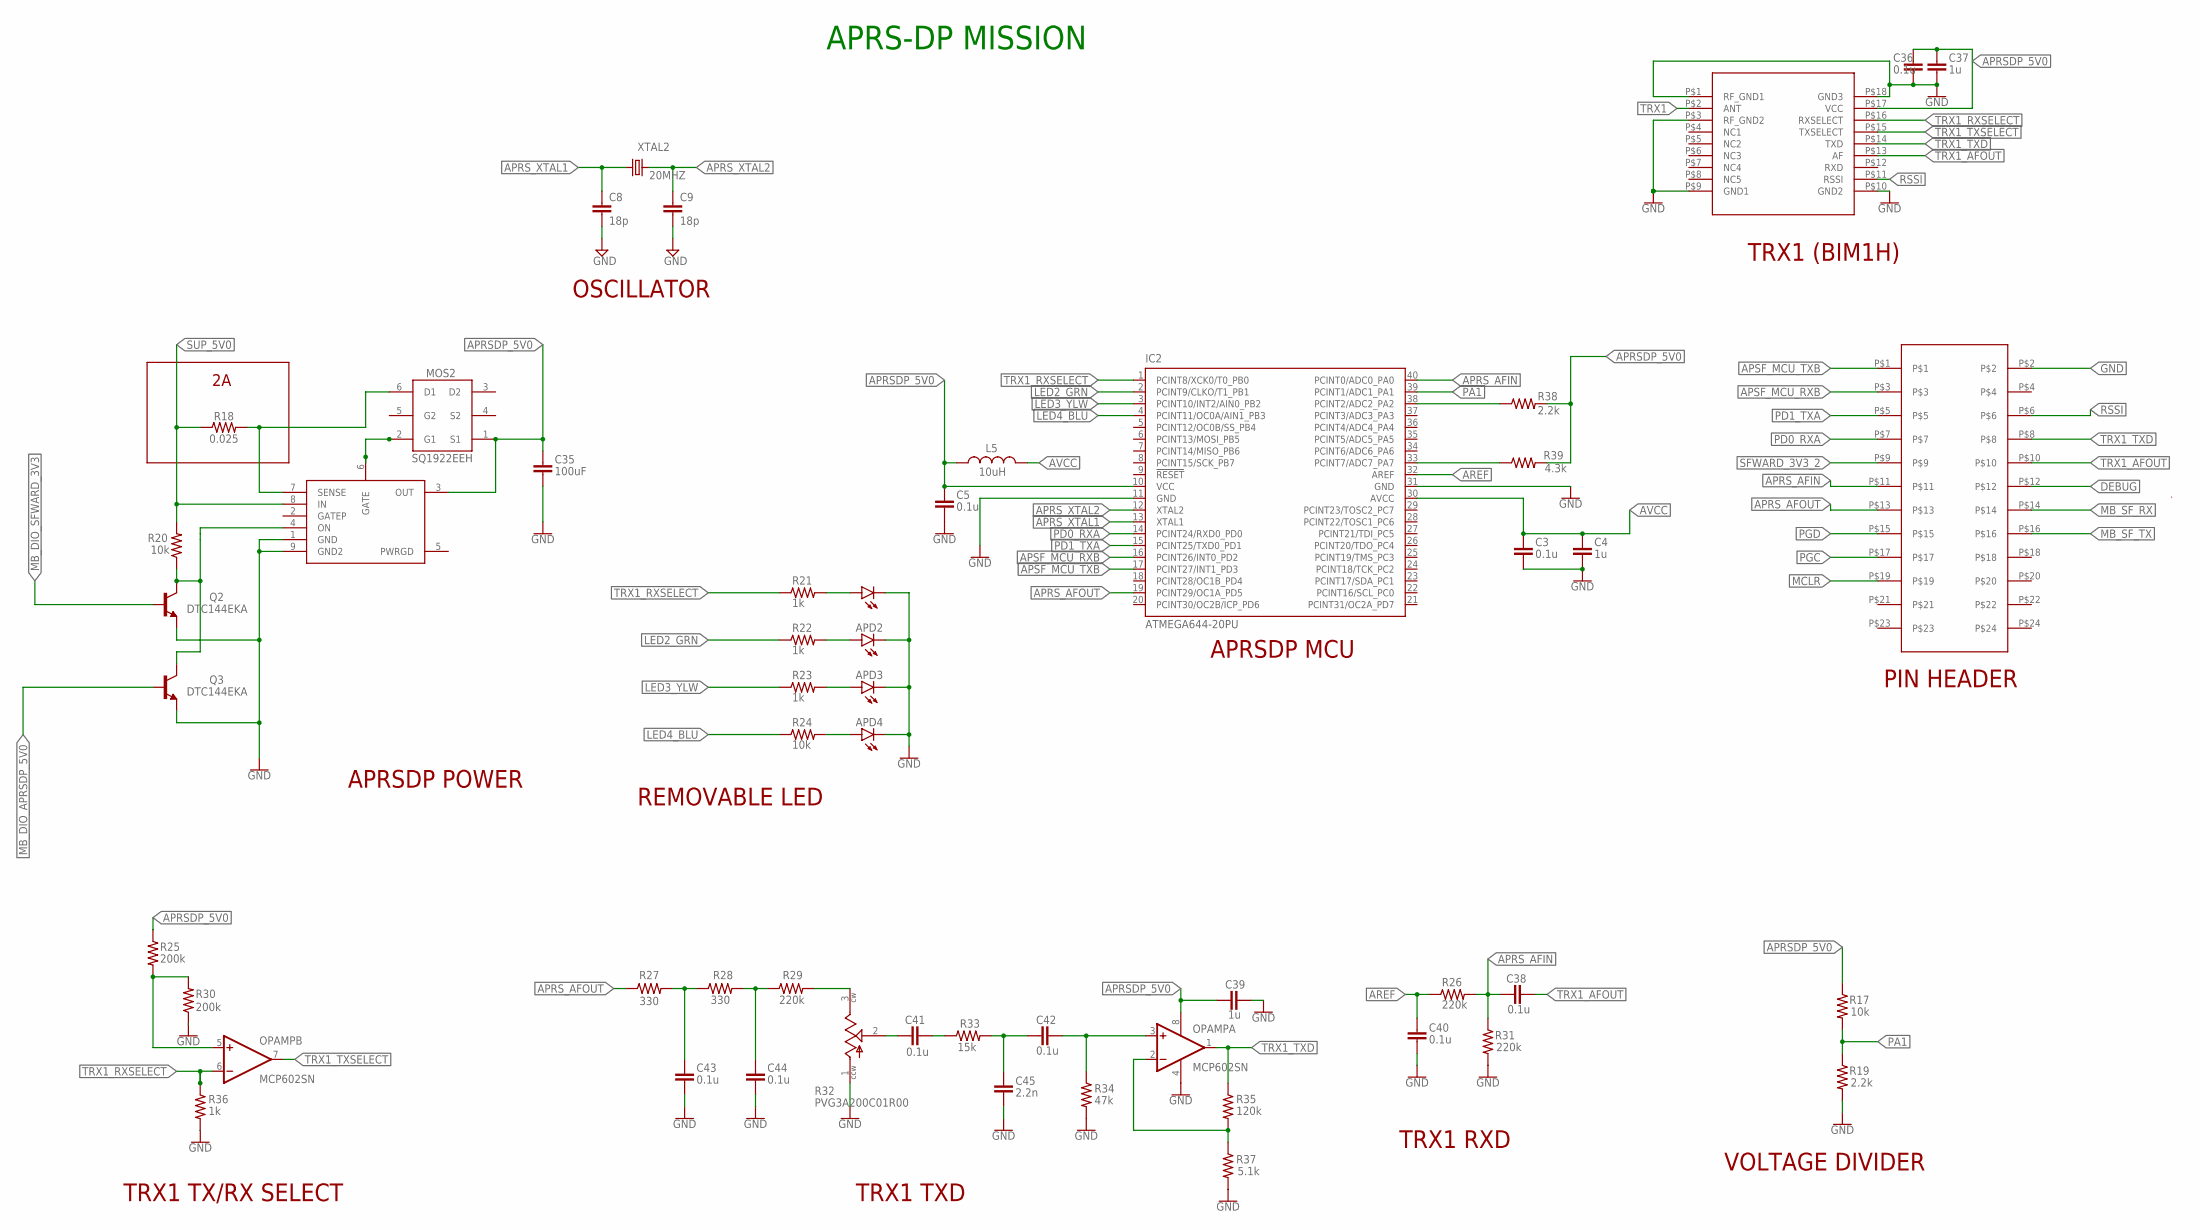
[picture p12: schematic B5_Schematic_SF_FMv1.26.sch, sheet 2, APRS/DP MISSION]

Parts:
APD1, APD2, APD3, APD4: LEDSML0603; SML0603
C3, C5, C36, C38, C40, C41, C42, C43, C44: 0.1u; C0603
C4, C37, C39: 1u; C0603
C8, C9: 18p; C0805
C35: 100uF; C0805
C45: 2.2n; C0603
IC2: ATMEGA644-20PU; DIL40
JP1: RAB_ACCESS
L5: 10uH; L2012C
MOS2: SQ1922EEH; SOT65P210X110-6N
OPAMP: MCP602SN; SO08
Q2, Q3: DTC144EKA; SOT346-R
R17, R20, R24: 10k; R0603
R18: 0.025; R0805
R19, R38: 2.2k; R0603
R21, R22, R23, R36: 1k; R0603
R25, R30: 200k; R0603
R26, R29, R31: 220k; R0603
R27, R28: 330; R0603
R32: PVG3A200C01R00; TRIM_PVG3A200C01R00
R33: 15k; R0603
R34: 47k; R0603
R35: 120k; R0603
R37: 5.1k; R0603
R39: 4.3k; R0603
TRX1: BIM1H
U$1: BIRDS5_LTC4361
XTAL2: 20MHZ; SM49

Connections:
APRSDP_5V0: C5.2, C35.1, C36.1, C37.1, C39.1, IC2.10 (VCC), L5.1, MOS2.1 (S1), OPAMP.8 (V+), R17.1, R25.1, R38.2, R39.2, TRX1.P$17 (VCC), U$1.3 (OUT)
APRS_AFIN: C38.1, IC2.40 (PCINT0/ADC0_PA0), JP1.P$11, R26.2, R31.1
APRS_AFOUT: IC2.19 (PCINT29/OC1A_PD5), JP1.P$13, R27.1
APRS_XTAL1: C8.1, IC2.13 (XTAL1), XTAL2.1
APRS_XTAL2: C9.1, IC2.12 (XTAL2), XTAL2.2
APSF_MCU_RXB: IC2.16 (PCINT26/INT0_PD2), JP1.P$3; also elsewhere on the board
APSF_MCU_TXB: IC2.17 (PCINT27/INT1_PD3), JP1.P$1; also elsewhere on the board
AREF: C40.1, IC2.32 (AREF), R26.1
AVCC: C3.1, C4.1, IC2.30 (AVCC), L5.2
DEBUG: JP1.P$12; also elsewhere on the board
GATE4: MOS2.2 (G1), U$1.6 (GATE)
GND: APD1.C, APD2.C, APD3.C, APD4.C, C3.2, C4.2, C5.1, C8.2, C9.2, C35.2, C36.2, C37.2, C39.2, C40.2, C43.2, C44.2, C45.2, IC2.11 (GND), IC2.31 (GND), JP1.P$2, OPAMP.4 (V-), Q2.1 (E), Q3.1 (E), R19.2, R30.1, R31.2, R32.1 (CCW), R34.2, R36.2, R37.2, TRX1.P$1 (RF_GND1), TRX1.P$3 (RF_GND2), TRX1.P$9 (GND1), TRX1.P$10 (GND2), TRX1.P$18 (GND3), U$1.1 (GND), U$1.9 (GND2); also elsewhere on the board
LED2_GRN: IC2.2 (PCINT9/CLKO/T1_PB1), R22.1
LED3_YLW: IC2.3 (PCINT10/INT2/AIN0_PB2), R23.1
LED4_BLU: IC2.4 (PCINT11/OC0A/AIN1_PB3), R24.1
MB_DIO_APRSDP_5V0: Q3.2 (B); also elsewhere on the board
MB_DIO_SFWARD_3V3: Q2.2 (B); also elsewhere on the board
MB_SF_RX: JP1.P$14; also elsewhere on the board
MB_SF_TX: JP1.P$16; also elsewhere on the board
MCLR: JP1.P$19; also elsewhere on the board
unnamed: R29.2, R32.3 (CW)
unnamed: APD1.A, R21.2
unnamed: APD2.A, R22.2
unnamed: APD3.A, R23.2
unnamed: APD4.A, R24.2
unnamed: C43.1, R27.2, R28.1
unnamed: C44.1, R28.2, R29.1
unnamed: C42.1, C45.1, R33.2
unnamed: C41.2, R33.1
unnamed: OPAMP.2 (-IN), R35.2, R37.1
unnamed: OPAMP.5 (+IN), R25.2, R30.2
unnamed: C41.1, R32.2 (WIPER)
unnamed: IC2.38 (PCINT2/ADC2_PA2), R38.1
unnamed: IC2.33 (PCINT7/ADC7_PA7), R39.1
ON4: Q2.3 (C), Q3.3 (C), R20.1, U$1.4 (ON)
OPAMP_A+: C42.2, OPAMP.3 (+IN), R34.1
PA1: IC2.39 (PCINT1/ADC1_PA1), R17.2, R19.1
PD0_RXA: IC2.14 (PCINT24/RXD0_PD0), JP1.P$7; also elsewhere on the board
PD1_TXA: IC2.15 (PCINT25/TXD0_PD1), JP1.P$5; also elsewhere on the board
PGC: JP1.P$17; also elsewhere on the board
PGD: JP1.P$15; also elsewhere on the board
RSSI: JP1.P$6, TRX1.P$11 (RSSI); also elsewhere on the board
SENSE4: MOS2.6 (D1), R18.2, U$1.7 (SENSE)
SFWARD_3V3_2: JP1.P$9; also elsewhere on the board
SUP_5V0: R18.1, R20.2, U$1.8 (IN); also elsewhere on the board
TRX1: TRX1.P$2 (ANT); also elsewhere on the board
TRX1_AFOUT: C38.2, JP1.P$10, TRX1.P$13 (AF)
TRX1_RXSELECT: IC2.1 (PCINT8/XCK0/T0_PB0), OPAMP.6 (-IN), R21.1, R36.1, TRX1.P$16 (RXSELECT)
TRX1_TXD: JP1.P$8, OPAMP.1 (OUT), R35.1, TRX1.P$14 (TXD)
TRX1_TXSELECT: OPAMP.7 (OUT), TRX1.P$15 (TXSELECT)

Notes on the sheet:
OSCILLATOR
APRSDP POWER
PIN HEADER
TRX1 RXD
TRX1 (BIM1H)
VOLTAGE DIVIDER
REMOVABLE LED
APRS-DP MISSION
APRSDP MCU
TRX1 TXD
TRX1 TX/RX SELECT

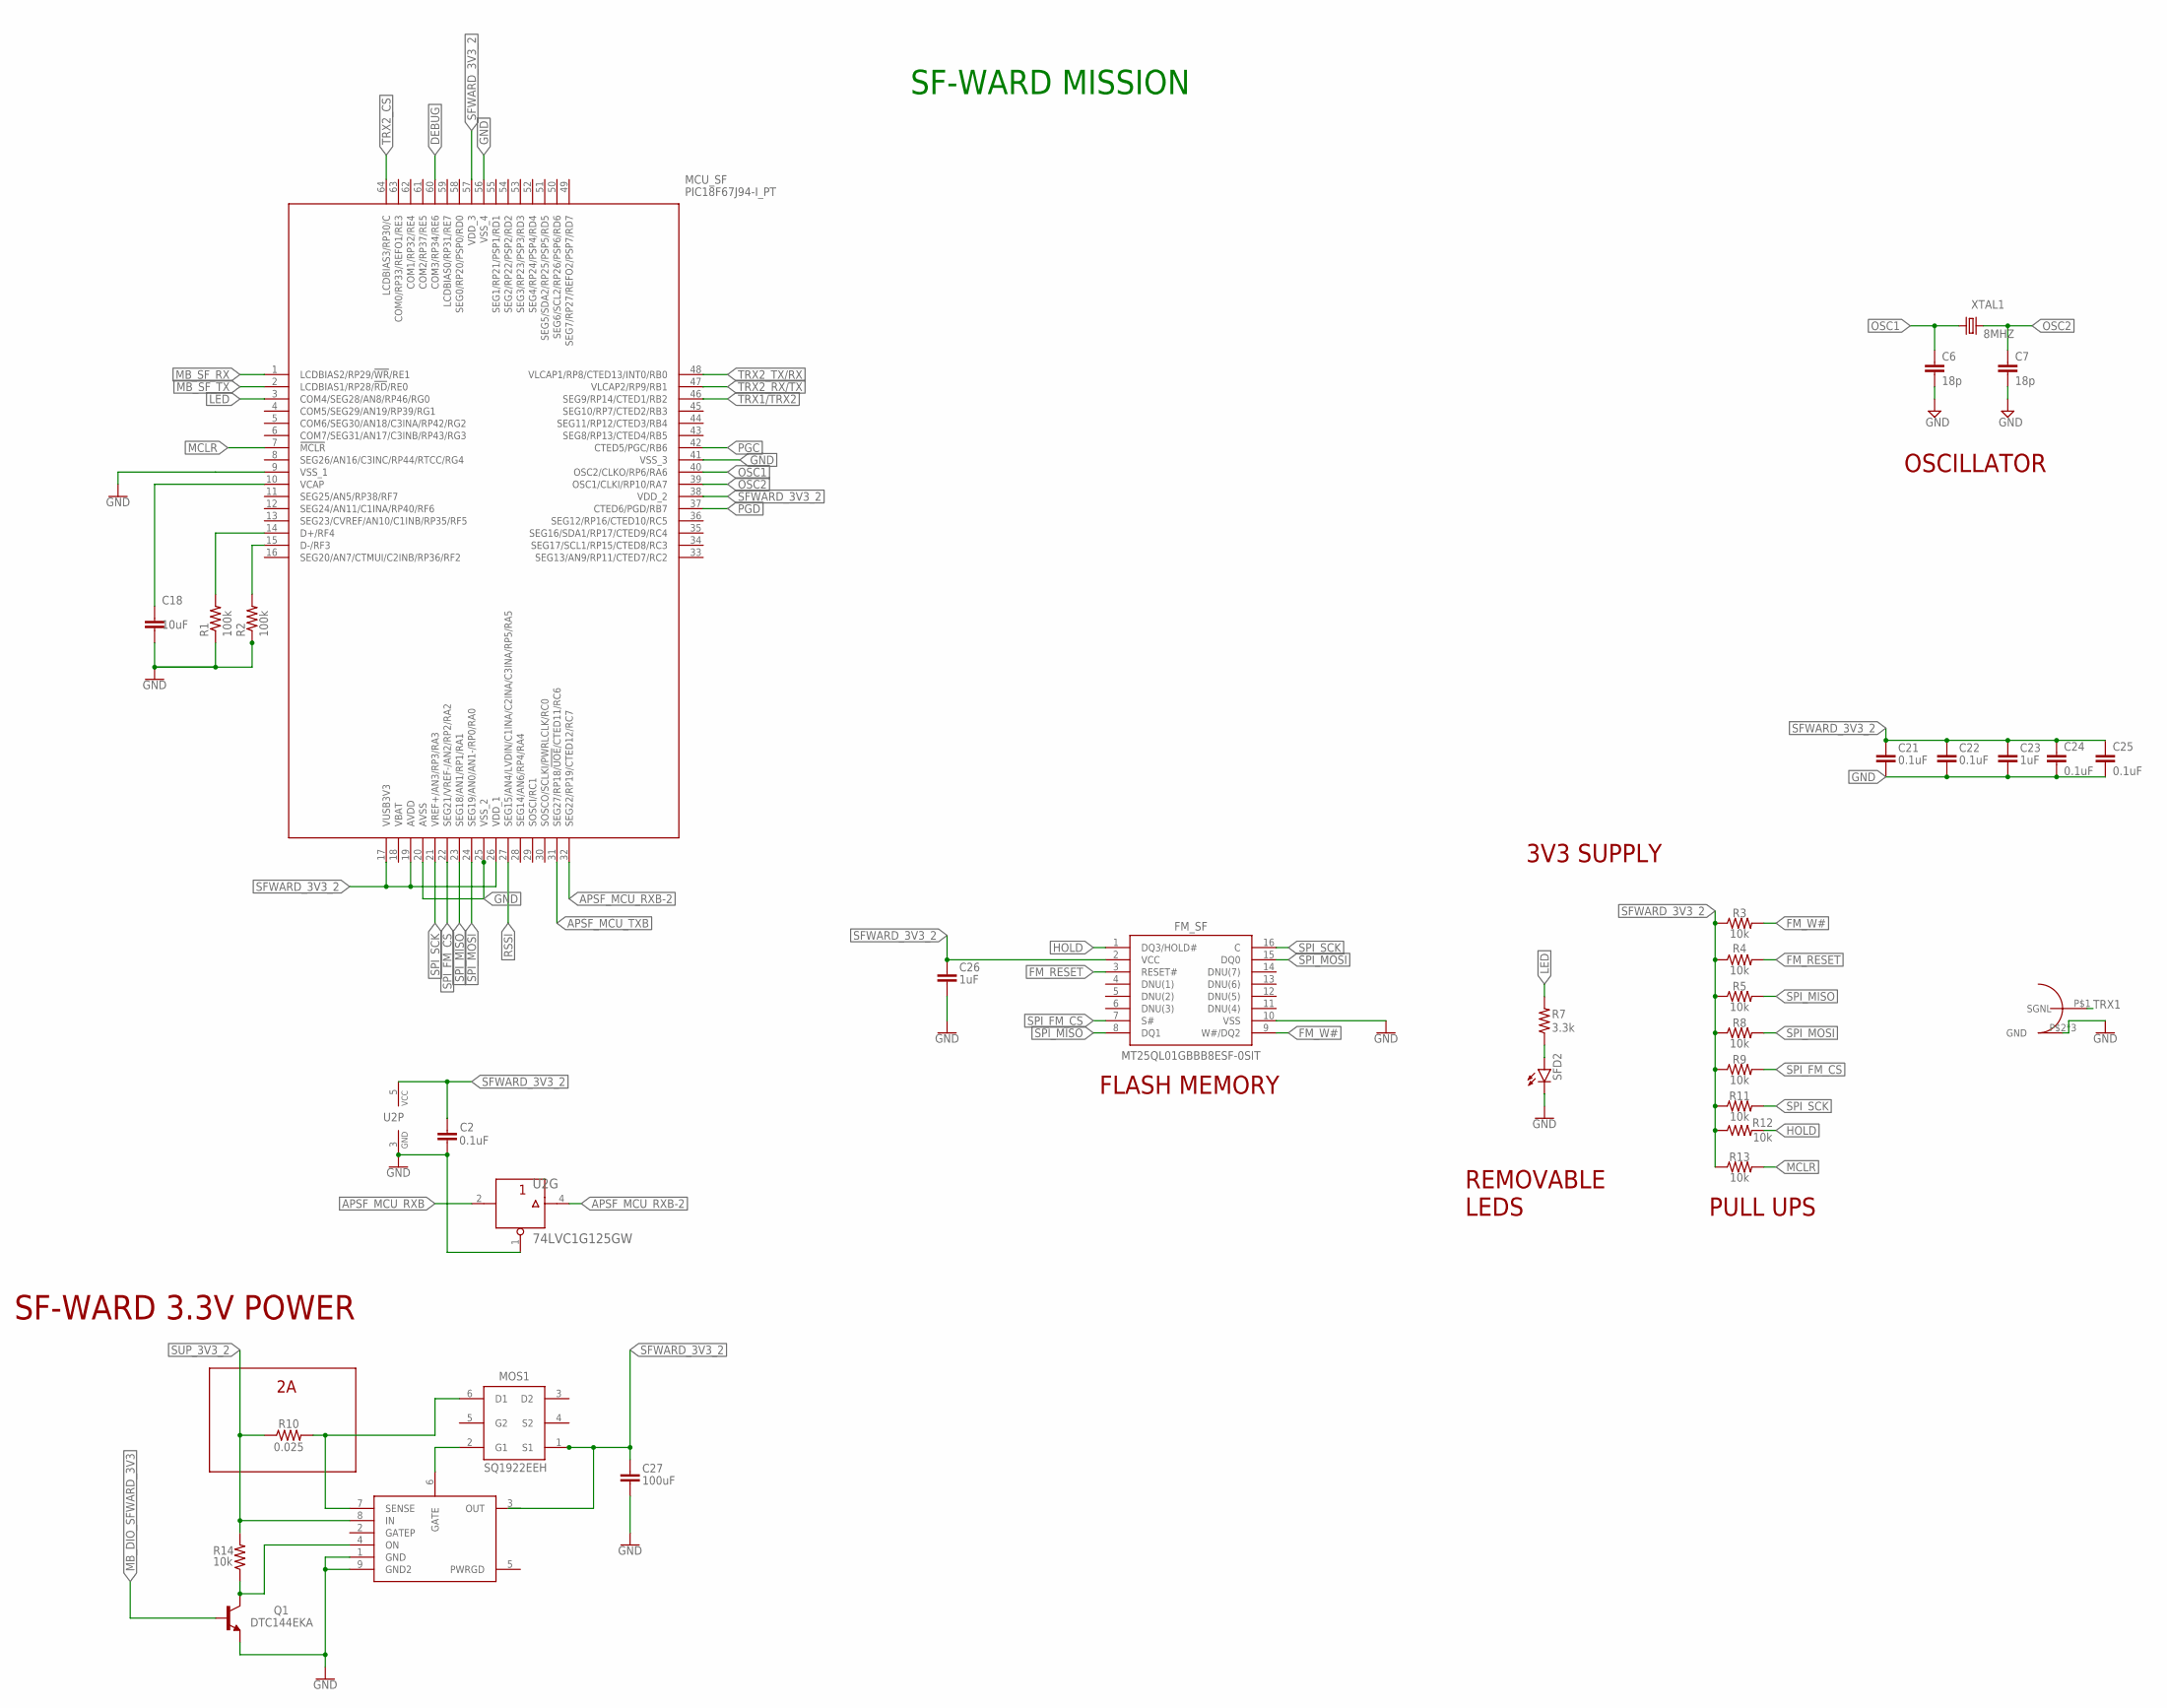
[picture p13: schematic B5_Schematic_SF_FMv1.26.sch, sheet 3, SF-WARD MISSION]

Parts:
C2, C21, C22, C24, C25: 0.1uF; C0603
C6, C7: 18p; C0805
C18: 10uF; C0603
C23, C26: 1uF; C0603
C27: 100uF; C0805
FM_SF: MT25QL01GBBB8ESF-0SIT; SOIC127P1032X265-16N
MCU_SF: PIC18F67J94-I_PT; QFP50P1200X1200X120-64N
MMCX_908_222101T: MMCX_908_222101T
MOS1: SQ1922EEH; SOT65P210X110-6N
Q1: DTC144EKA; SOT346-R
R1, R2: 100k; R0603
R3, R4, R5, R8, R9, R11, R12, R13, R14: 10k; R0603
R7: 3.3k; R0603
R10: 0.025; R0805
SFD2: LEDCHIPLED_0603; CHIPLED_0603
U2: 74LVC1G125GW; SOT353-1
U$3: BIRDS5_LTC4361
XTAL1: 8MHZ; SM49

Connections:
APSF_MCU_RXB: U2.2 (A); also elsewhere on the board
APSF_MCU_RXB-2: MCU_SF.32 (SEG22/RP19/CTED12/RC7), U2.4 (Y)
APSF_MCU_TXB: MCU_SF.31 (SEG27/RP18/!UOE!/CTED11/RC6); also elsewhere on the board
DEBUG: MCU_SF.60 (COM3/RP34/RE6); also elsewhere on the board
FM_RESET: FM_SF.3 (RESET#), R4.2
FM_W#: FM_SF.9 (W#/DQ2), R3.2
GATE3: MOS1.2 (G1), U$3.6 (GATE)
GND: C2.1, C6.2, C7.2, C18.2, C21.2, C22.2, C23.2, C24.2, C25.2, C26.2, C27.2, FM_SF.10 (VSS), MCU_SF.9 (VSS_1), MCU_SF.20 (AVSS), MCU_SF.25 (VSS_2), MCU_SF.41 (VSS_3), MCU_SF.56 (VSS_4), MMCX_908_222101T.P$2 (GND), MMCX_908_222101T.P$3 (GND), MMCX_908_222101T.P$4 (GND), Q1.1 (E), R1.1, R2.1, SFD2.C, U2.1 (OEN), U2.3 (GND), U$3.1 (GND), U$3.9 (GND2); also elsewhere on the board
HOLD: FM_SF.1 (DQ3/HOLD#), R12.2
LED: MCU_SF.3 (COM4/SEG28/AN8/RP46/RG0), R7.2
MB_DIO_SFWARD_3V3: Q1.2 (B); also elsewhere on the board
MB_SF_RX: MCU_SF.1 (LCDBIAS2/RP29/!WR!/RE1); also elsewhere on the board
MB_SF_TX: MCU_SF.2 (LCDBIAS1/RP28/!RD!/RE0); also elsewhere on the board
MCLR: MCU_SF.7 (!MCLR), R13.2; also elsewhere on the board
unnamed: C18.1, MCU_SF.10 (VCAP)
unnamed: MCU_SF.14 (D+/RF4), R1.2
unnamed: MCU_SF.15 (D-/RF3), R2.2
unnamed: R7.1, SFD2.A
ON3: Q1.3 (C), R14.1, U$3.4 (ON)
OSC1: C6.1, MCU_SF.40 (OSC2/CLKO/RP6/RA6), XTAL1.1
OSC2: C7.1, MCU_SF.39 (OSC1/CLKI/RP10/RA7), XTAL1.2
PGC: MCU_SF.42 (CTED5/PGC/RB6); also elsewhere on the board
PGD: MCU_SF.37 (CTED6/PGD/RB7); also elsewhere on the board
RSSI: MCU_SF.27 (SEG15/AN4/LVDIN/C1INA/C2INA/C3INA/RP5/R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); also elsewhere on the board
SENSE3: MOS1.6 (D1), R10.2, U$3.7 (SENSE)
SFWARD_3V3_2: C2.2, C21.1, C22.1, C23.1, C24.1, C25.1, C26.1, C27.1, FM_SF.2 (VCC), MCU_SF.17 (VUSB3V3), MCU_SF.19 (AVDD), MCU_SF.26 (VDD_1), MCU_SF.38 (VDD_2), MCU_SF.57 (VDD_3), MOS1.1 (S1), R3.1, R4.1, R5.1, R8.1, R9.1, R11.1, R12.1, R13.1, U2.5 (VCC), U$3.3 (OUT); also elsewhere on the board
SPI_FM_CS: FM_SF.7 (S#), MCU_SF.22 (SEG21/VREF-/AN2/RP2/RA2), R9.2
SPI_MISO: FM_SF.8 (DQ1), MCU_SF.23 (SEG18/AN1/RP1/RA1), R5.2
SPI_MOSI: FM_SF.15 (DQ0), MCU_SF.24 (SEG19/AN0/AN1-/RP0/RA0), R8.2
SPI_SCK: FM_SF.16 (C), MCU_SF.21 (VREF+/AN3/RP3/RA3), R11.2
SUP_3V3_2: R10.1, R14.2, U$3.8 (IN); also elsewhere on the board
TRX1: MMCX_908_222101T.P$1 (SGNL); also elsewhere on the board
TRX1/TRX2: MCU_SF.46 (SEG9/RP14/CTED1/RB2)
TRX2_CS: MCU_SF.64 (LCDBIAS3/RP30/C)
TRX2_RX/TX: MCU_SF.47 (VLCAP2/RP9/RB1)
TRX2_TX/RX: MCU_SF.48 (VLCAP1/RP8/CTED13/INT0/RB0)

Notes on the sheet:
FLASH MEMORY
SF-WARD 3.3V POWER
PULL UPS
REMOVABLE LEDS
OSCILLATOR
3V3 SUPPLY
SF-WARD MISSION

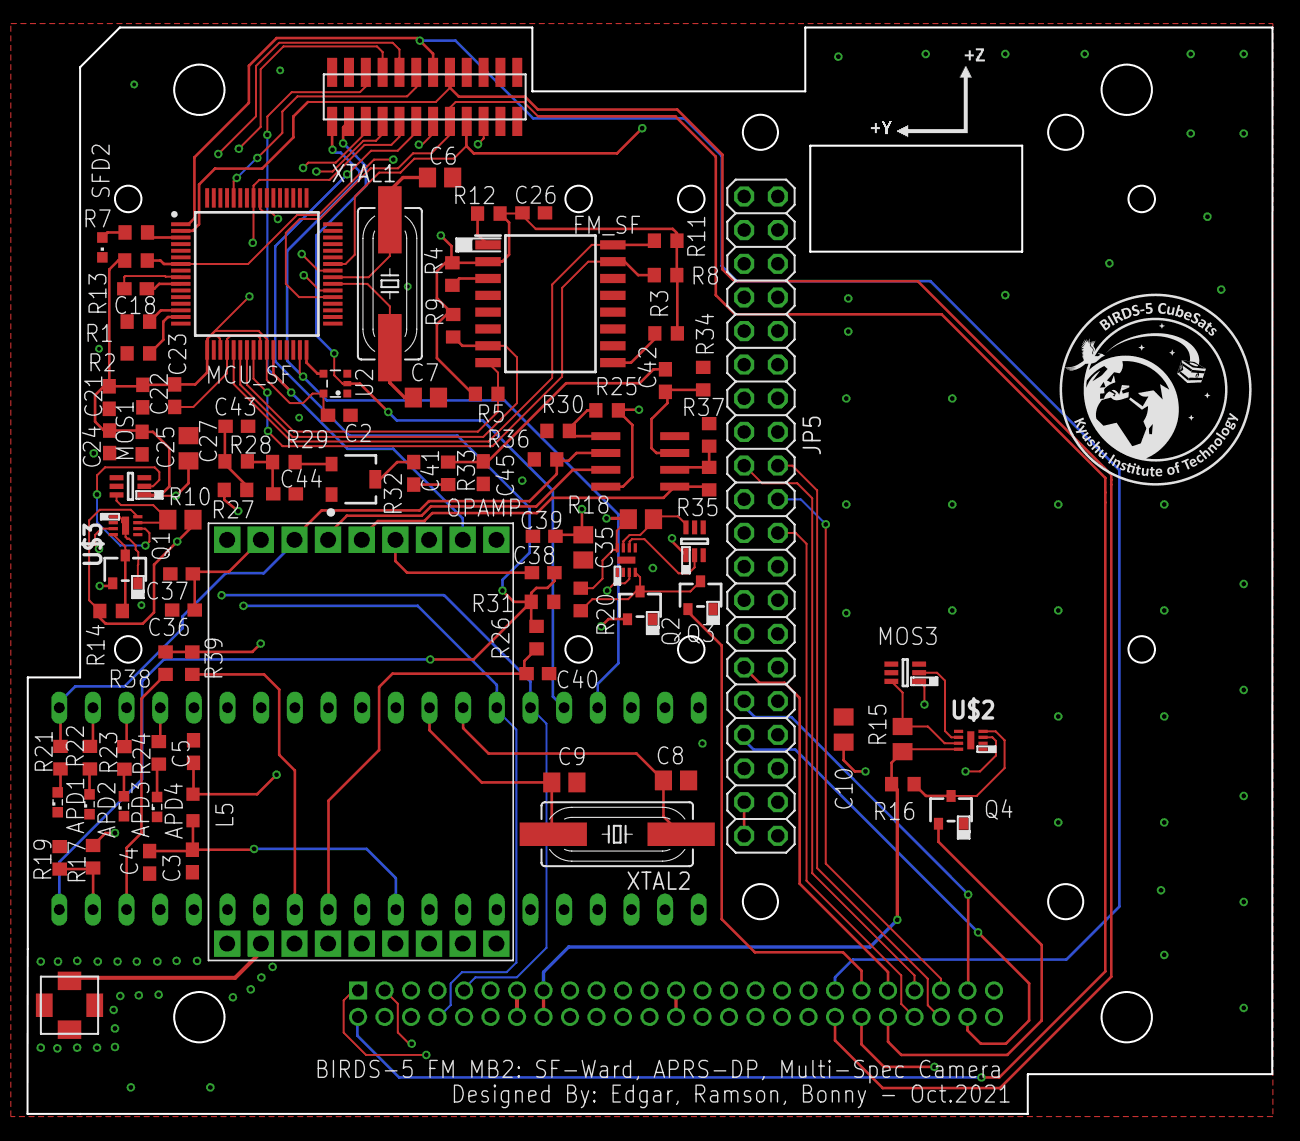
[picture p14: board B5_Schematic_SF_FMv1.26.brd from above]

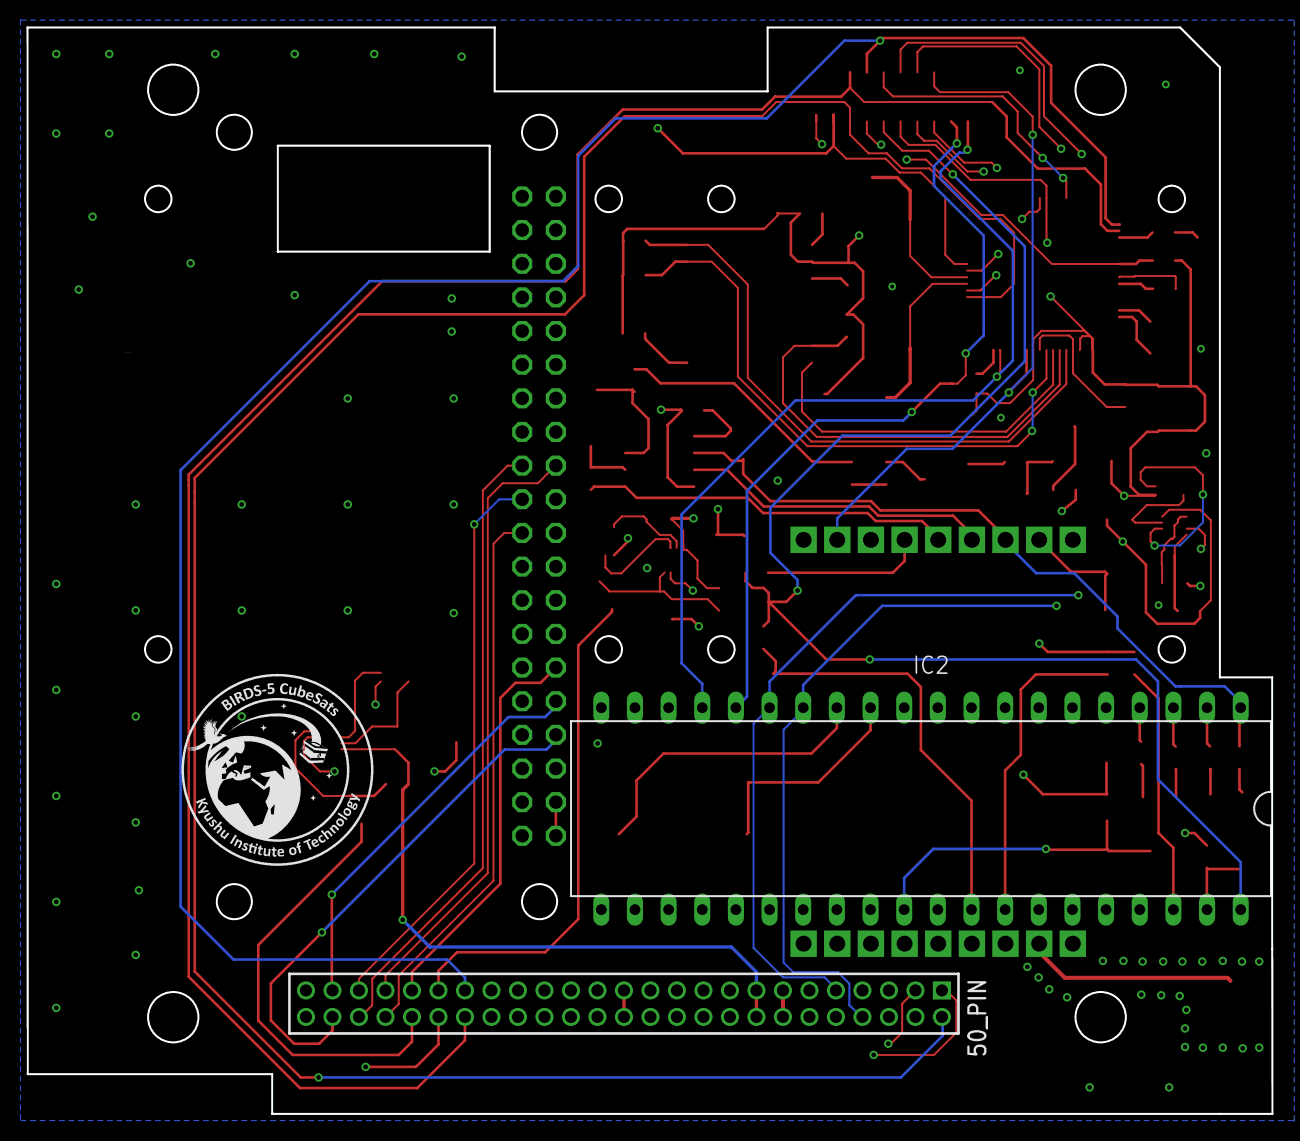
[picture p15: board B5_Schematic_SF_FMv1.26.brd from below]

Board: 4 copper layers, 94.0 x 82.0 mm, 94 parts (2 on the bottom side), 81 nets.

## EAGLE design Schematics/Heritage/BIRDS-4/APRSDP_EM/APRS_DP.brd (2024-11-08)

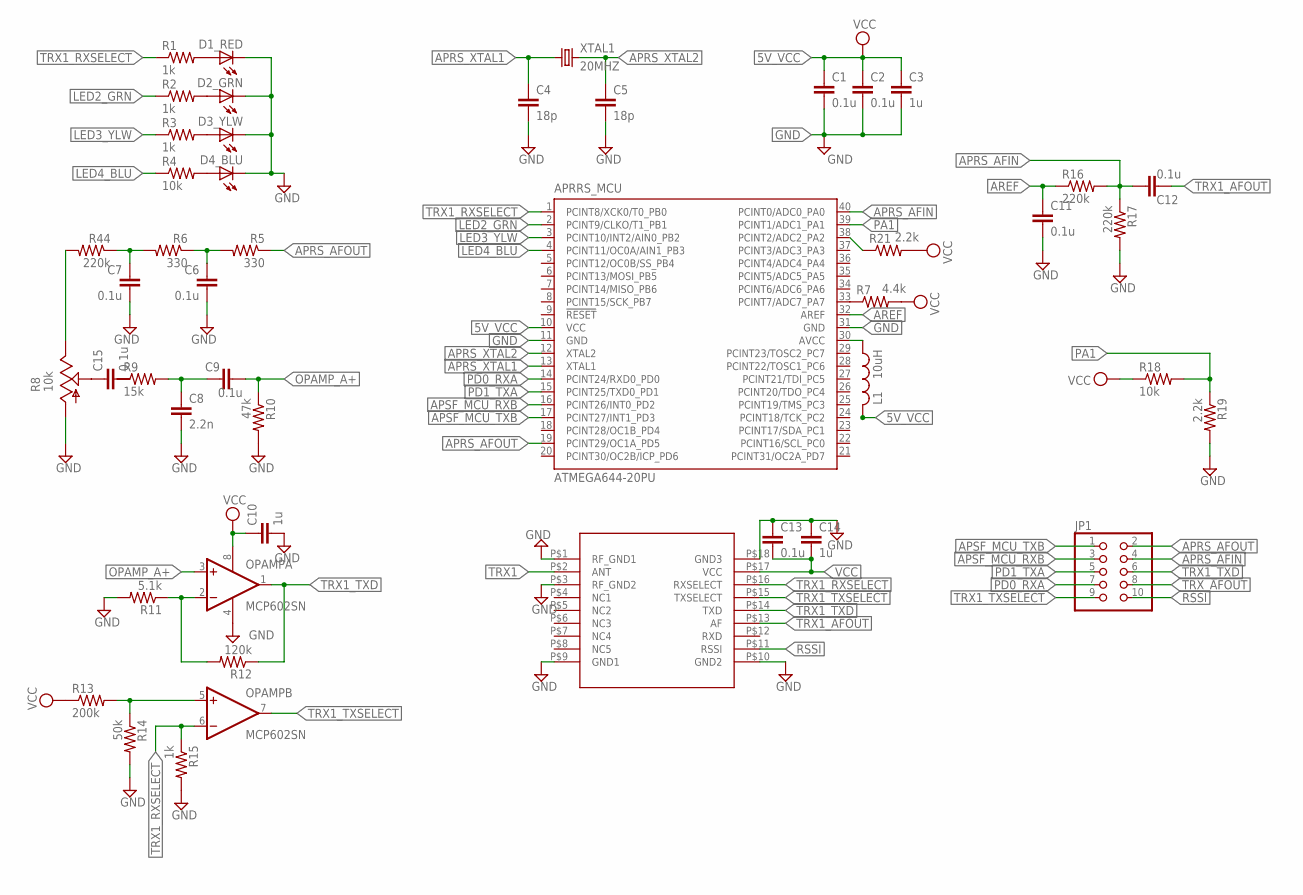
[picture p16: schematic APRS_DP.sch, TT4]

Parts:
APRRS_MCU: ATMEGA644-20PU; DIL40
BIM1H(TRX1)1: BIM1H
C1, C2, C6, C7, C9, C11, C12, C13, C15: 0.1u; C0805
C3, C10, C14: 1u; C0805
C4, C5: 18p; C0805
C8: 2.2n; C0805
D1_RED, D2_GRN, D3_YLW, D4_BLU: LEDSML0805; SML0805
JP1: PINHD-2X5; 2X05
L1: 10uH; L2012C
OPAMP: MCP602SN; SO08
R1, R2, R3, R15: 1k; R0805
R4, R18: 10k; R0805
R5, R6: 330; R0805
R7: 4.4k; R0805
R8: 10k; 3223W
R9: 15k; R0805
R10: 47k; R0805
R11: 5.1k; R0805
R12: 120k; R0805
R13: 200k; R0805
R14: 50k; R0805
R16, R17, R44: 220k; R0805
R19, R21: 2.2k; R0805
XTAL1: 20MHZ; SM49

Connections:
5V_VCC: APRRS_MCU.10 (VCC), C1.1, C2.1, C3.1, L1.2
APRS_AFIN: APRRS_MCU.40 (PCINT0/ADC0_PA0), C12.1, JP1.4, R16.2, R17.1
APRS_AFOUT: APRRS_MCU.19 (PCINT29/OC1A_PD5), JP1.2, R5.1
APRS_XTAL1: APRRS_MCU.13 (XTAL1), C4.1, XTAL1.1
APRS_XTAL2: APRRS_MCU.12 (XTAL2), C5.1, XTAL1.2
APSF_MCU_RXB: APRRS_MCU.16 (PCINT26/INT0_PD2), JP1.3
APSF_MCU_TXB: APRRS_MCU.17 (PCINT27/INT1_PD3), JP1.1
AREF: APRRS_MCU.32 (AREF), C11.1, R16.1
GND: APRRS_MCU.11 (GND), APRRS_MCU.31 (GND), BIM1H(TRX1)1.P$1 (RF_GND1), BIM1H(TRX1)1.P$3 (RF_GND2), BIM1H(TRX1)1.P$9 (GND1), BIM1H(TRX1)1.P$10 (GND2), BIM1H(TRX1)1.P$18 (GND3), C1.2, C2.2, C3.2, C4.2, C5.2, C6.2, C7.2, C8.2, C10.2, C11.2, C13.1, C14.1, D1_RED.C, D2_GRN.C, D3_YLW.C, D4_BLU.C, OPAMP.4 (V-), R8.1 (A), R10.2, R11.2, R14.2, R15.2, R17.2, R19.2
LED2_GRN: APRRS_MCU.2 (PCINT9/CLKO/T1_PB1), R2.1
LED3_YLW: APRRS_MCU.3 (PCINT10/INT2/AIN0_PB2), R3.1
LED4_BLU: APRRS_MCU.4 (PCINT11/OC0A/AIN1_PB3), R4.1
unnamed: APRRS_MCU.30 (AVCC), L1.1
unnamed: C6.1, R5.2, R6.1
unnamed: D1_RED.A, R1.2
unnamed: D2_GRN.A, R2.2
unnamed: D3_YLW.A, R3.2
unnamed: D4_BLU.A, R4.2
unnamed: OPAMP.2 (-IN), R11.1, R12.2
unnamed: C15.1, R8.2 (S)
unnamed: APRRS_MCU.33 (PCINT7/ADC7_PA7), R7.1
unnamed: C7.1, R6.2, R44.1
unnamed: C8.1, C9.1, R9.2
unnamed: R8.3 (E), R44.2
OPAMP_A+: C9.2, OPAMP.3 (+IN), R10.1
OPAMP_B+: OPAMP.5 (+IN), R13.2, R14.1
PA1: APRRS_MCU.39 (PCINT1/ADC1_PA1), R18.2, R19.1
PA2: APRRS_MCU.38 (PCINT2/ADC2_PA2), R21.1
PD0_RXA: APRRS_MCU.14 (PCINT24/RXD0_PD0), JP1.7
PD1_TXA: APRRS_MCU.15 (PCINT25/TXD0_PD1), JP1.5
RSSI: BIM1H(TRX1)1.P$11 (RSSI), JP1.10
TRX1: BIM1H(TRX1)1.P$2 (ANT)
TRX1_AFOUT: BIM1H(TRX1)1.P$13 (AF), C12.2
TRX1_RXSELECT: APRRS_MCU.1 (PCINT8/XCK0/T0_PB0), BIM1H(TRX1)1.P$16 (RXSELECT), OPAMP.6 (-IN), R1.1, R15.1
TRX1_TXD: BIM1H(TRX1)1.P$14 (TXD), JP1.6, OPAMP.1 (OUT), R12.1
TRX1_TXSELECT: BIM1H(TRX1)1.P$15 (TXSELECT), JP1.9, OPAMP.7 (OUT)
TRX_AFOUT: JP1.8
VCC: BIM1H(TRX1)1.P$17 (VCC), C10.1, C13.2, C14.2, OPAMP.8 (V+), R7.2, R13.1, R18.1, R21.2

Board: 4 copper layers, 46 parts (0 on the bottom side), 36 nets, no tracks yet.

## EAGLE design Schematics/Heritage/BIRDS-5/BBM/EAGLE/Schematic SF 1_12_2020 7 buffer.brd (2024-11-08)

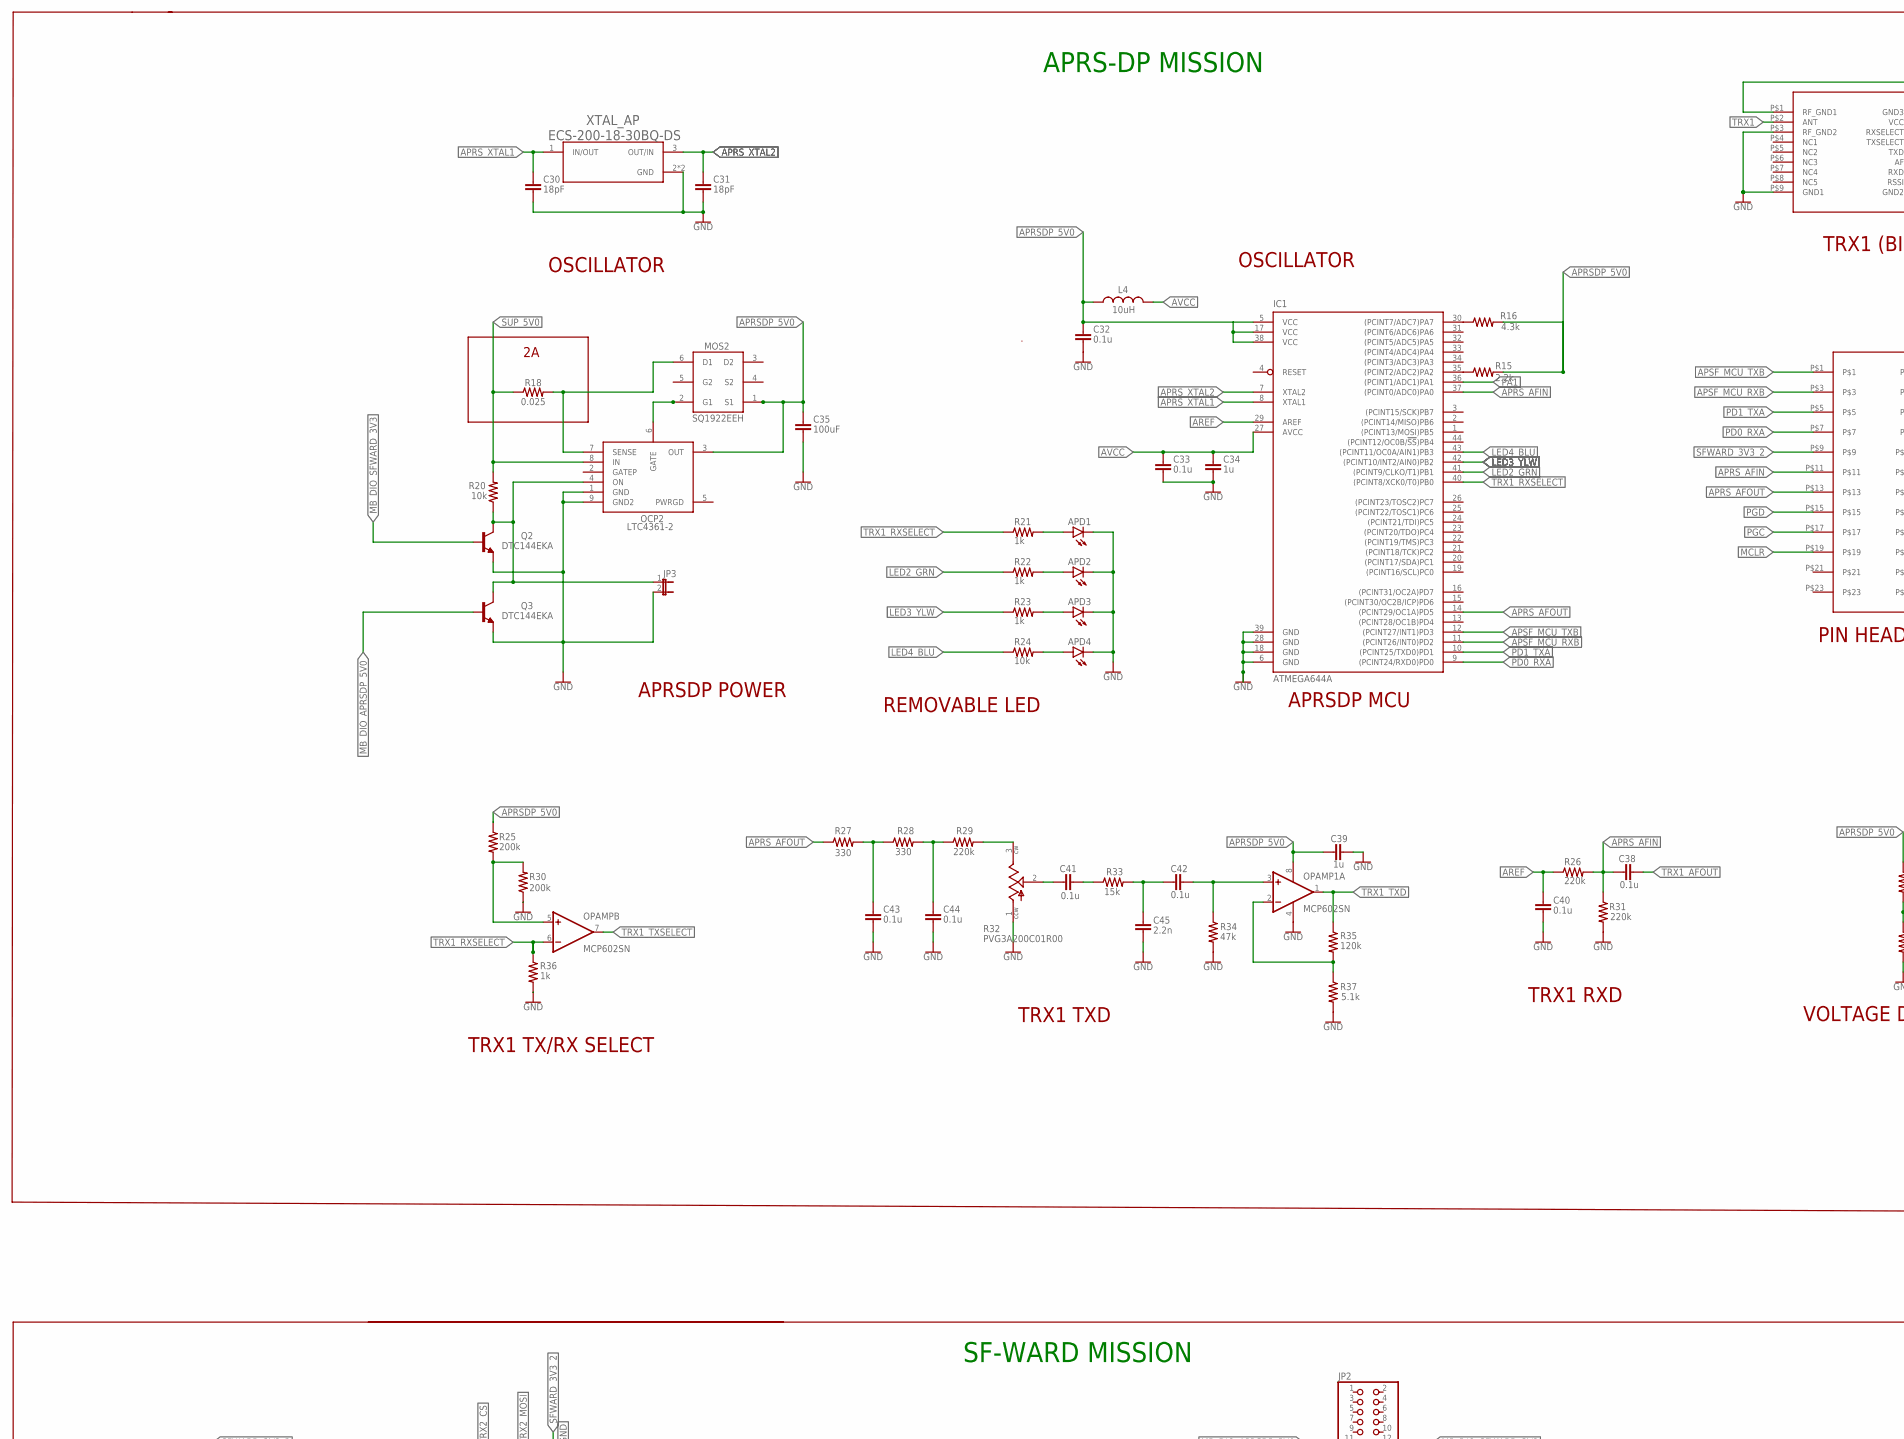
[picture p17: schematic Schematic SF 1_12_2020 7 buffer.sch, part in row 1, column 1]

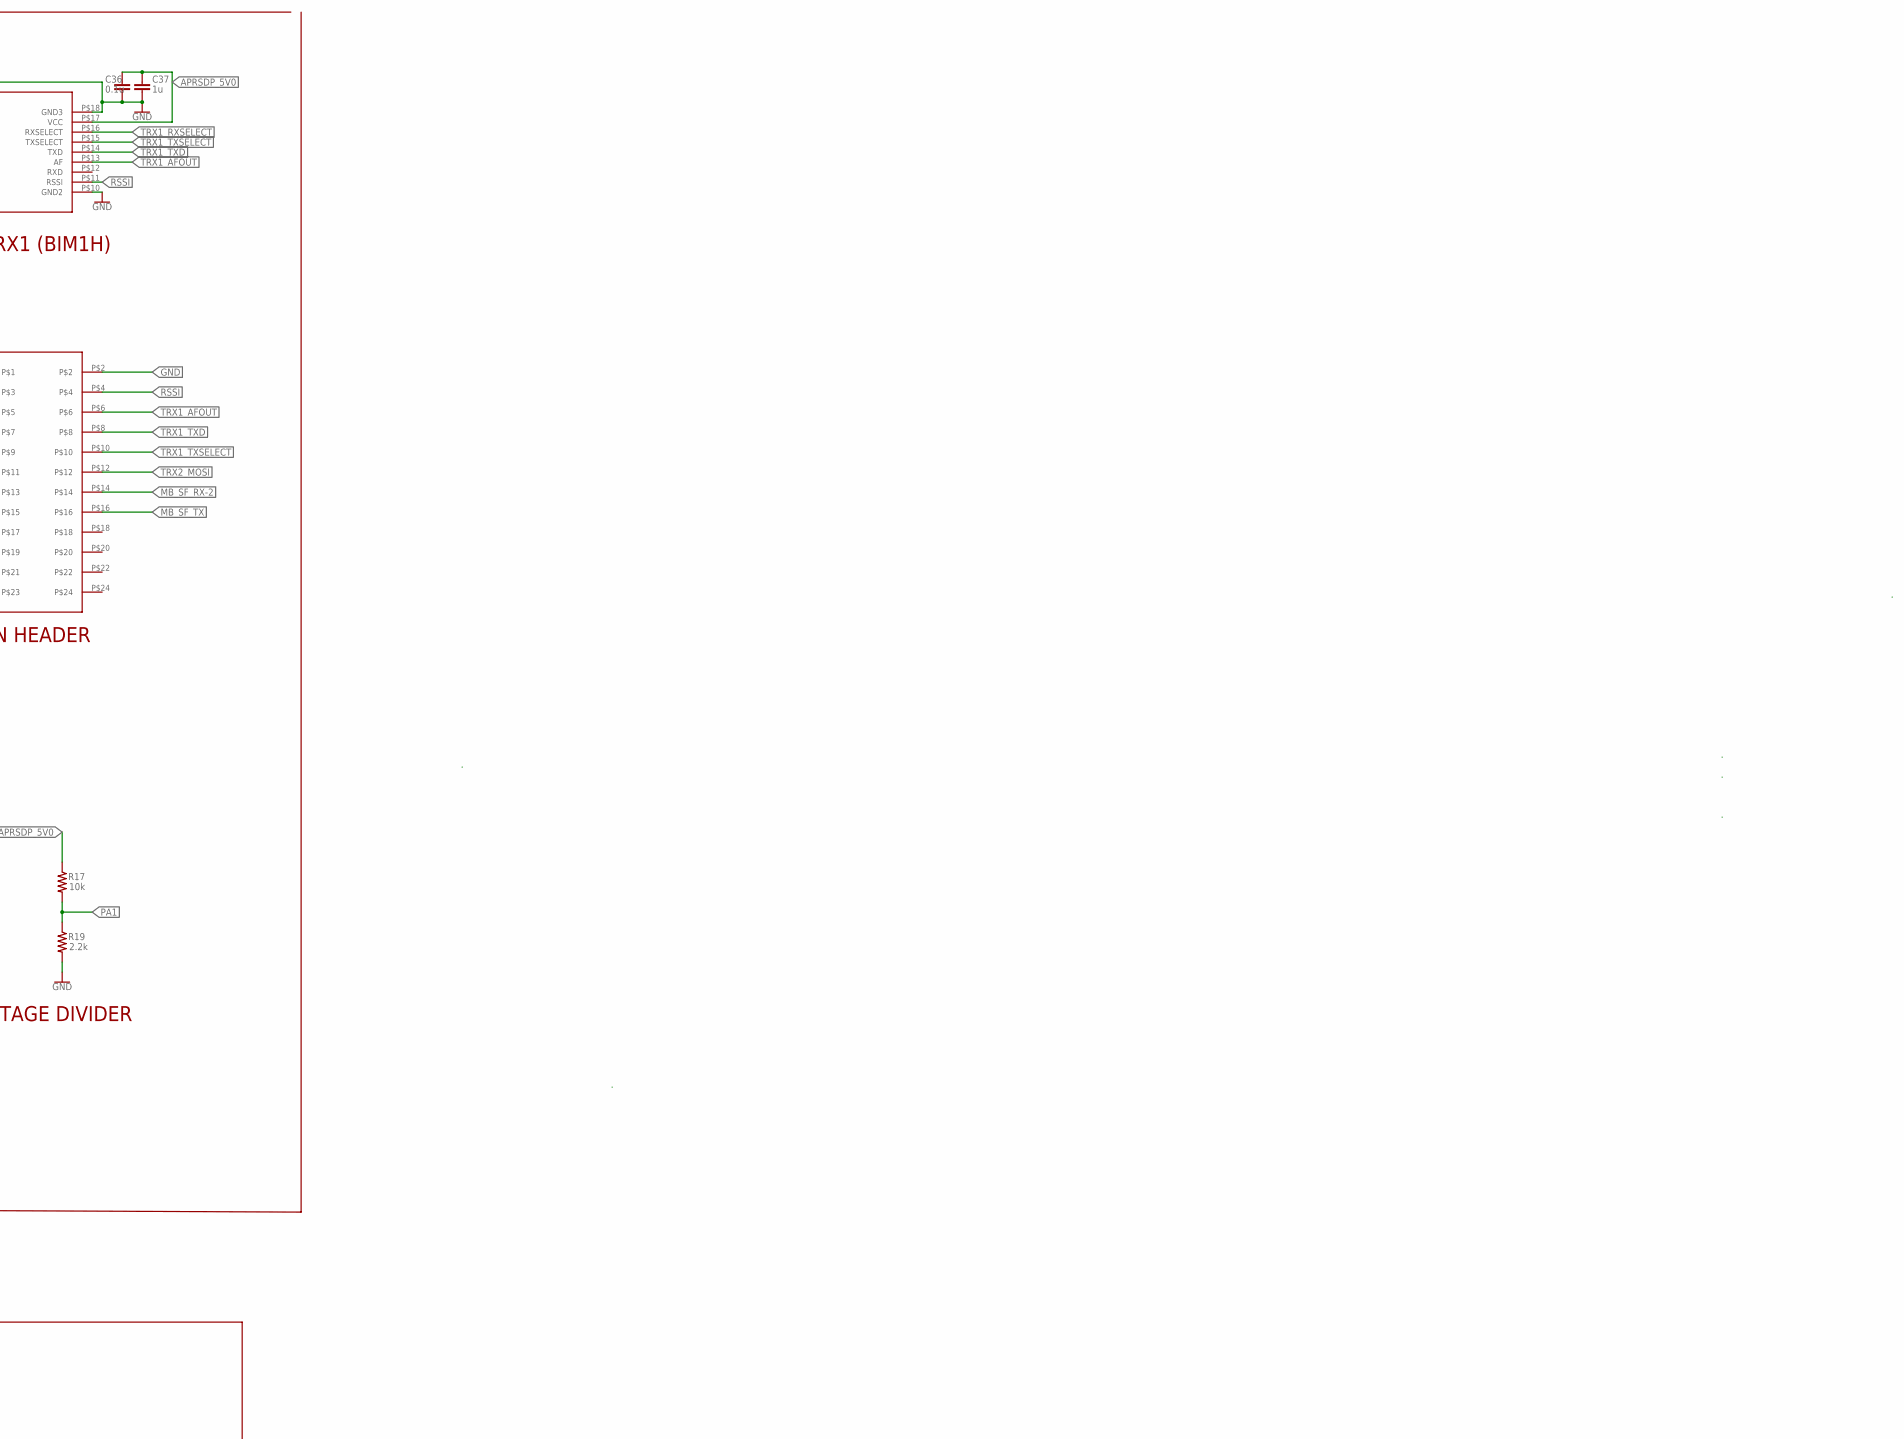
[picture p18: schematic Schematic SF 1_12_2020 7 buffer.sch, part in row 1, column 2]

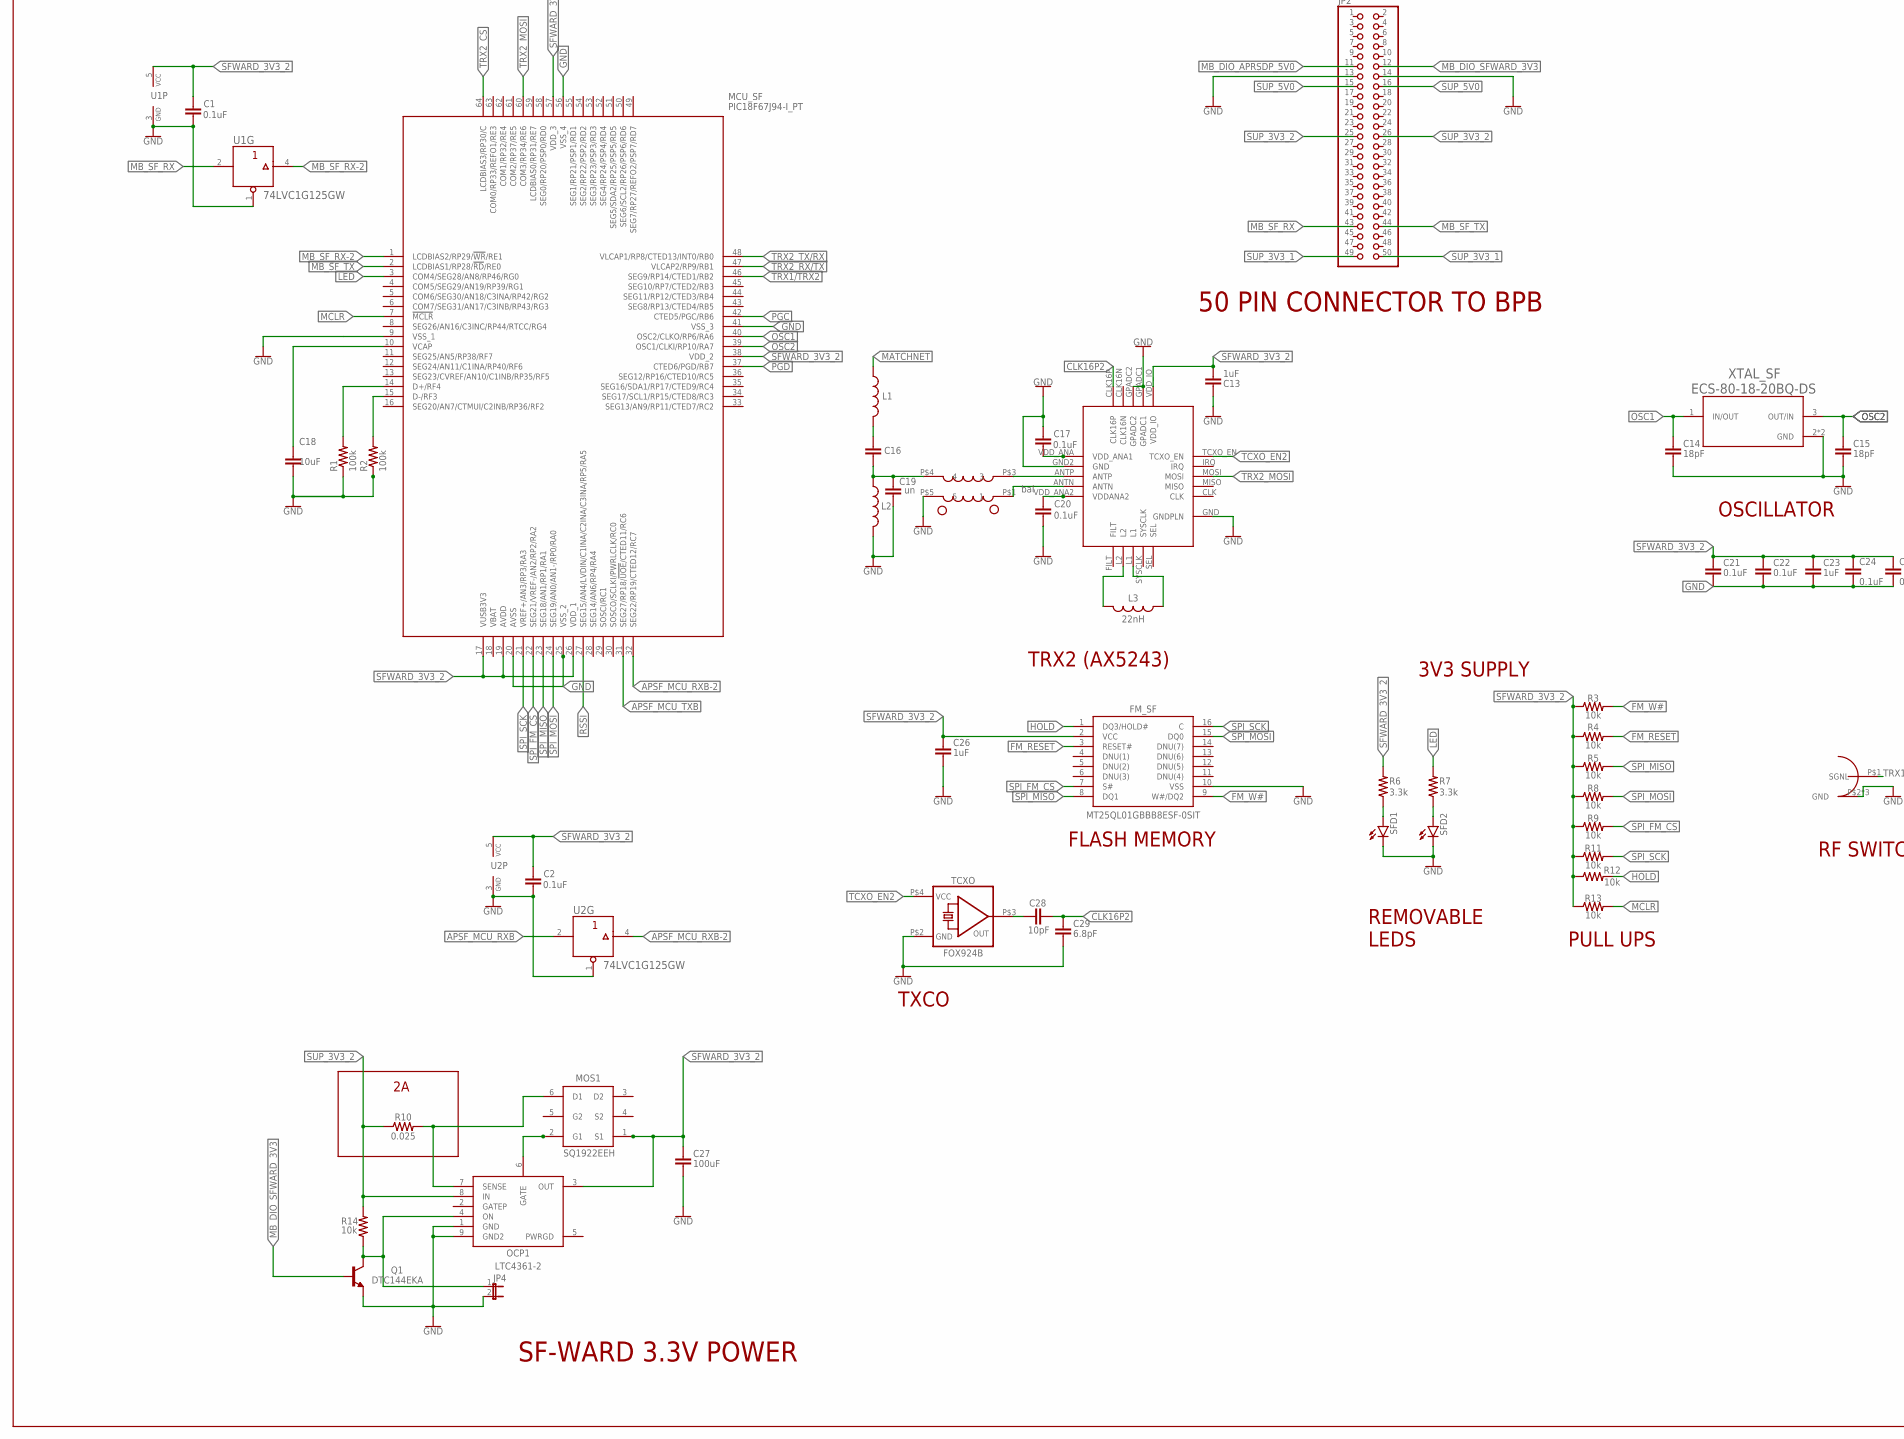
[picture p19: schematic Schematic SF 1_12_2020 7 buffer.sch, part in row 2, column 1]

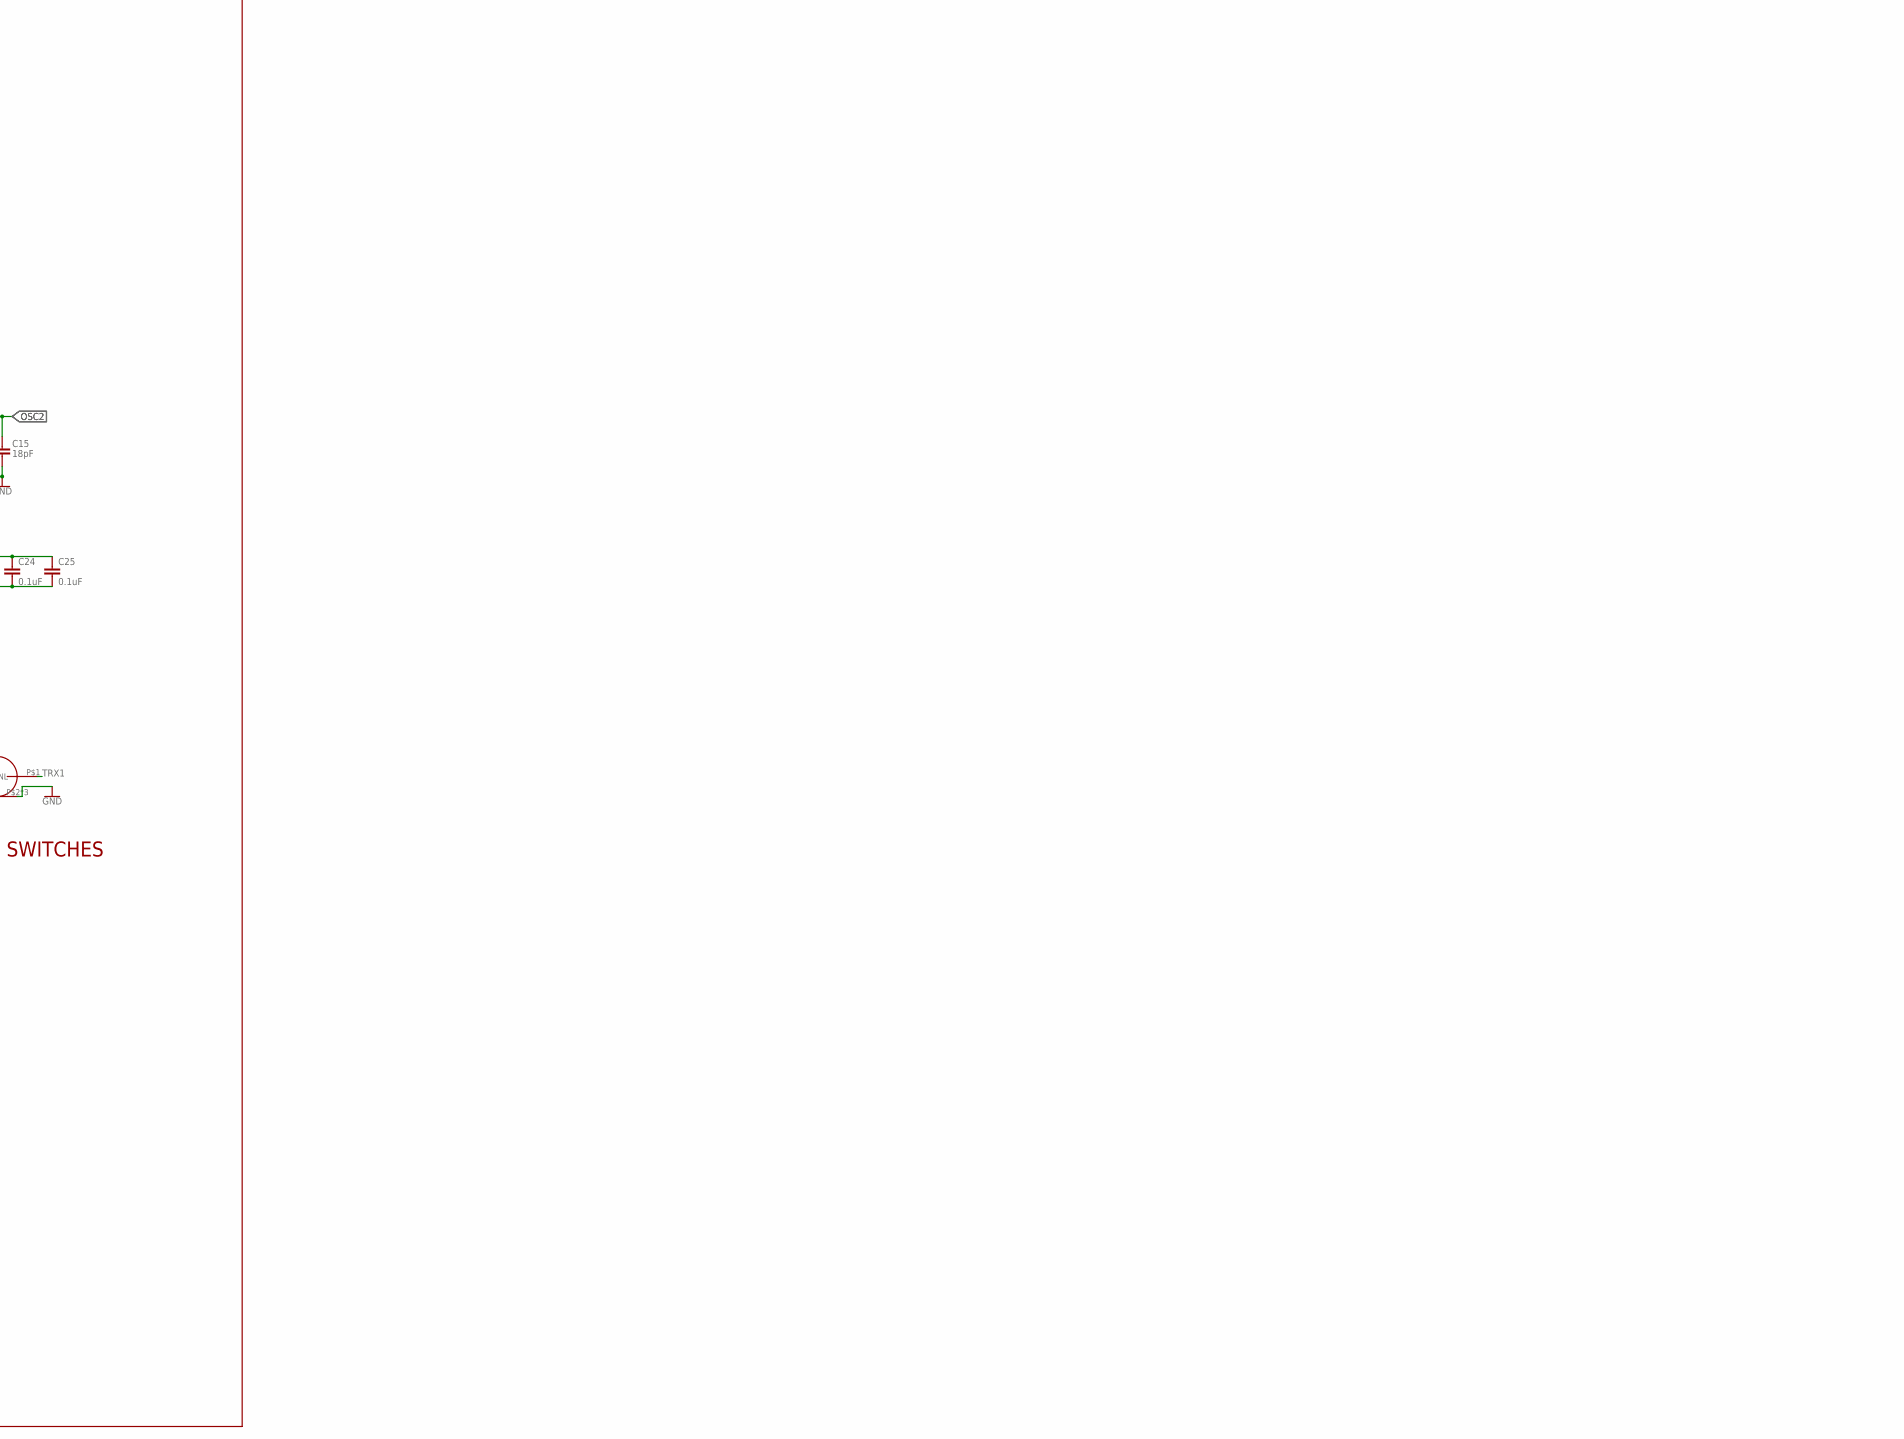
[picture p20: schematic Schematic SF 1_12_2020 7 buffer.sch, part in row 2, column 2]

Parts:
APD1, APD2, APD3, APD4: LEDSML0603; SML0603
BAL: MABA-010245-BALUN
C1, C2, C17, C20, C21, C22, C24, C25: 0.1uF; C0603
C13, C23, C26: 1uF; C0603
C14, C15, C30, C31: 18pF; C0603
C16, C19: C-EUC0805; C0805
C18: 10uF; C0603
C27, C35: 100uF; C0805
C28: 10pF; C0603
C29: 6.8pF; C0603
C32, C33, C36, C38, C40, C41, C42, C43, C44: 0.1u; C0603
C34, C37, C39: 1u; C0603
C45: 2.2n; C0603
FM_SF: MT25QL01GBBB8ESF-0SIT; SOIC127P1032X265-16N
IC1: ATMEGA644A; TQFP44
JP1: RAB_ACCESS
JP2: PINHD-2X25_2.00; 2X25M
JP3, JP4: JP1E; JP1
L1, L2: L-USL2012C; L2012C
L3: 22nH; L2012C
L4: 10uH; L2012C
MCU_SF: PIC18F67J94-I_PT; QFP50P1200X1200X120-64N
MOS1, MOS2: SQ1922EEH; SOT65P210X110-6N
OCP1, OCP2: LTC4361-2; DFN
OPAMP, OPAMP1: MCP602SN; SO08
Q1, Q2, Q3: DTC144EKA; SOT346-R
R1, R2: 100k; R0603
R3, R4, R5, R8, R9, R11, R12, R13, R14, R17, R20, R24: 10k; R0603
R6, R7: 3.3k; R0603
R10, R18: 0.025; R0805
R15, R19: 2.2k; R0603
R16: 4.3k; R0603
R21, R22, R23, R36: 1k; R0603
R25, R30: 200k; R0603
R26, R29, R31: 220k; R0603
R27, R28: 330; R0603
R32: PVG3A200C01R00; TRIM_PVG3A200C01R00
R33: 15k; R0603
R34: 47k; R0603
R35: 120k; R0603
R37: 5.1k; R0603
RFCON: MMCX_908_222101T
SFD1, SFD2: LEDCHIPLED_0603; CHIPLED_0603
TCXO: FOX924B
TRX1: BIM1H
TRX2: AX5243
U1, U2: 74LVC1G125GW; SOT353-1
XTAL_AP: ECS-200-18-30BQ-DS; XTAL_ECS-200-18-30BQ-DS
XTAL_SF: ECS-80-18-20BQ-DS; XTAL_ECS-80-18-20BQ-DS

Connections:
APRSDP_5V0: C32.2, C35.1, C36.1, C37.1, C39.1, L4.1, MOS2.1 (S1), OCP2.3 (OUT), OPAMP1.8 (V+), R15.2, R16.2, R17.1, R25.1, TRX1.P$17 (VCC)
APRS_AFIN: C38.1, IC1.37 ((PCINT0/ADC0)PA0), JP1.P$11, R26.2, R31.1
APRS_AFOUT: IC1.14 ((PCINT29/OC1A)PD5), JP1.P$13, R27.1
APRS_XTAL1: C30.1, IC1.8 (XTAL1), XTAL_AP.1 (IN/OUT)
APRS_XTAL2: C31.1, IC1.7 (XTAL2), XTAL_AP.3 (OUT/IN)
APSF_MCU_RXB: IC1.11 ((PCINT26/INT0)PD2), JP1.P$3, U2.2 (A)
APSF_MCU_RXB-2: MCU_SF.32 (SEG22/RP19/CTED12/RC7), U2.4 (Y)
APSF_MCU_TXB: IC1.12 ((PCINT27/INT1)PD3), JP1.P$1, MCU_SF.31 (SEG27/RP18/!UOE!/CTED11/RC6)
AREF: C40.1, IC1.29 (AREF), R26.1
AVCC: C33.1, C34.1, IC1.27 (AVCC), L4.2
CLK16P2: C28.2, C29.1, TRX2.CLK16P
FM_RESET: FM_SF.3 (RESET#), R4.2
FM_W#: FM_SF.9 (W#/DQ2), R3.2
GATE3: MOS1.2 (G1), OCP1.6 (GATE)
GATE4: MOS2.2 (G1), OCP2.6 (GATE)
GND: APD1.C, APD2.C, APD3.C, APD4.C, BAL.P$5 (5), C1.1, C2.1, C13.1, C14.2, C15.2, C17.2, C18.2, C19.2, C20.2, C21.2, C22.2, C23.2, C24.2, C25.2, C26.2, C27.2, C29.2, C30.2, C31.2, C32.1, C33.2, C34.2, C35.2, C36.2, C37.2, C39.2, C40.2, C43.2, C44.2, C45.2, FM_SF.10 (VSS), IC1.6 (GND), IC1.18 (GND), IC1.28 (GND), IC1.39 (GND), JP1.P$2, JP2.13, JP2.14, JP3.2, JP4.2, L2.2, MCU_SF.9 (VSS_1), MCU_SF.20 (AVSS), MCU_SF.25 (VSS_2), MCU_SF.41 (VSS_3), MCU_SF.56 (VSS_4), OCP1.1 (GND), OCP1.9 (GND2), OCP2.1 (GND), OCP2.9 (GND2), OPAMP1.4 (V-), Q1.1 (E), Q2.1 (E), Q3.1 (E), R1.1, R2.1, R19.2, R30.1, R31.2, R32.1 (CCW), R34.2, R36.2, R37.2, RFCON.P$2 (GND), RFCON.P$3 (GND), RFCON.P$4 (GND), SFD1.C, SFD2.C, TCXO.P$2 (GND), TRX1.P$1 (RF_GND1), TRX1.P$3 (RF_GND2), TRX1.P$9 (GND1), TRX1.P$10 (GND2), TRX1.P$18 (GND3), TRX2.GND (GNDPLN), TRX2.GND2 (GND), TRX2.GPADC1, TRX2.GPADC2, U1.1 (OEN), U1.3 (GND), U2.1 (OEN), U2.3 (GND), XTAL_AP.2 (GND), XTAL_AP.4 (GND), XTAL_SF.2 (GND), XTAL_SF.4 (GND)
HOLD: FM_SF.1 (DQ3/HOLD#), R12.2
LED: MCU_SF.3 (COM4/SEG28/AN8/RP46/RG0), R7.2
LED2_GRN: IC1.41 ((PCINT9/CLKO/T1)PB1), R22.1
LED3_YLW: IC1.42 ((PCINT10/INT2/AIN0)PB2), R23.1
LED4_BLU: IC1.43 ((PCINT11/OC0A/AIN1)PB3), R24.1
MATCHNET: L1.1
MB_DIO_APRSDP_5V0: JP2.11, Q3.2 (B)
MB_DIO_SFWARD_3V3: JP2.12, Q1.2 (B), Q2.2 (B)
MB_SF_RX: JP2.43, U1.2 (A)
MB_SF_RX-2: JP1.P$14, MCU_SF.1 (LCDBIAS2/RP29/!WR!/RE1), U1.4 (Y)
MB_SF_TX: JP1.P$16, JP2.44, MCU_SF.2 (LCDBIAS1/RP28/!RD!/RE0)
MCLR: JP1.P$19, MCU_SF.7 (!MCLR), R13.2
unnamed: C18.1, MCU_SF.10 (VCAP)
unnamed: IC1.5 (VCC), IC1.17 (VCC), IC1.38 (VCC)
unnamed: IC1.35 ((PCINT2/ADC2)PA2), R15.1
unnamed: IC1.30 ((PCINT7/ADC7)PA7), R16.1
unnamed: MCU_SF.14 (D+/RF4), R1.2
unnamed: MCU_SF.15 (D-/RF3), R2.2
unnamed: R6.1, SFD1.A
unnamed: R29.2, R32.3 (CW)
unnamed: R7.1, SFD2.A
unnamed: APD1.A, R21.2
unnamed: APD2.A, R22.2
unnamed: APD3.A, R23.2
unnamed: APD4.A, R24.2
unnamed: C43.1, R27.2, R28.1
unnamed: C44.1, R28.2, R29.1
unnamed: C42.1, C45.1, R33.2
unnamed: C41.2, R33.1
unnamed: OPAMP1.2 (-IN), R35.2, R37.1
unnamed: OPAMP.5 (+IN), R25.2, R30.2
unnamed: C41.1, R32.2 (WIPER)
unnamed: C20.1, TRX2.VDD_ANA2 (VDDANA2)
unnamed: C17.1, TRX2.VDD_ANA (VDD_ANA1)
unnamed: L3.2, TRX2.L2
unnamed: L3.1, TRX2.L1
unnamed: C16.1, L1.2
unnamed: BAL.P$4 (4), C16.2, C19.1, L2.1
unnamed: BAL.P$1 (1), TRX2.ANTN
unnamed: BAL.P$3 (3), TRX2.ANTP
unnamed: C28.1, TCXO.P$3 (OUT)
ON3: JP4.1, OCP1.4 (ON), Q1.3 (C), R14.1
ON4: JP3.1, OCP2.4 (ON), Q2.3 (C), Q3.3 (C), R20.1
OPAMP_A+: C42.2, OPAMP1.3 (+IN), R34.1
OSC1: C14.1, MCU_SF.40 (OSC2/CLKO/RP6/RA6), XTAL_SF.1 (IN/OUT)
OSC2: C15.1, MCU_SF.39 (OSC1/CLKI/RP10/RA7), XTAL_SF.3 (OUT/IN)
PA1: IC1.36 ((PCINT1/ADC1)PA1), R17.2, R19.1
PD0_RXA: IC1.9 ((PCINT24/RXD0)PD0), JP1.P$7
PD1_TXA: IC1.10 ((PCINT25/TXD0)PD1), JP1.P$5
PGC: JP1.P$17, MCU_SF.42 (CTED5/PGC/RB6)
PGD: JP1.P$15, MCU_SF.37 (CTED6/PGD/RB7)
RSSI: JP1.P$4, MCU_SF.27 (SEG15/AN4/LVDIN/C1INA/C2INA/C3INA/RP5/R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), TRX1.P$11 (RSSI)
SENSE3: MOS1.6 (D1), OCP1.7 (SENSE), R10.2
SENSE4: MOS2.6 (D1), OCP2.7 (SENSE), R18.2
SFWARD_3V3_2: C1.2, C2.2, C13.2, C21.1, C22.1, C23.1, C24.1, C25.1, C26.1, C27.1, FM_SF.2 (VCC), JP1.P$9, MCU_SF.17 (VUSB3V3), MCU_SF.19 (AVDD), MCU_SF.26 (VDD_1), MCU_SF.38 (VDD_2), MCU_SF.57 (VDD_3), MOS1.1 (S1), OCP1.3 (OUT), R3.1, R4.1, R5.1, R6.2, R8.1, R9.1, R11.1, R12.1, R13.1, TRX2.VDD_IO, U1.5 (VCC), U2.5 (VCC)
SPI_FM_CS: FM_SF.7 (S#), MCU_SF.22 (SEG21/VREF-/AN2/RP2/RA2), R9.2
SPI_MISO: FM_SF.8 (DQ1), MCU_SF.23 (SEG18/AN1/RP1/RA1), R5.2
SPI_MOSI: FM_SF.15 (DQ0), MCU_SF.24 (SEG19/AN0/AN1-/RP0/RA0), R8.2
SPI_SCK: FM_SF.16 (C), MCU_SF.21 (VREF+/AN3/RP3/RA3), R11.2
SUP_3V3_1: JP2.49, JP2.50
SUP_3V3_2: JP2.25, JP2.26, OCP1.8 (IN), R10.1, R14.2
SUP_5V0: JP2.15, JP2.16, OCP2.8 (IN), R18.1, R20.2
TCXO_EN2: TCXO.P$4 (VCC), TRX2.TCXO_EN
TRX1: RFCON.P$1 (SGNL), TRX1.P$2 (ANT)
TRX1/TRX2: MCU_SF.46 (SEG9/RP14/CTED1/RB2)
TRX1_AFOUT: C38.2, JP1.P$6, TRX1.P$13 (AF)
TRX1_RXSELECT: IC1.40 ((PCINT8/XCK0/T0)PB0), OPAMP.6 (-IN), R21.1, R36.1, TRX1.P$16 (RXSELECT)
TRX1_TXD: JP1.P$8, OPAMP1.1 (OUT), R35.1, TRX1.P$14 (TXD)
TRX1_TXSELECT: JP1.P$10, OPAMP.7 (OUT), TRX1.P$15 (TXSELECT)
TRX2_CS: MCU_SF.64 (LCDBIAS3/RP30/C)
TRX2_MOSI: JP1.P$12, MCU_SF.60 (COM3/RP34/RE6), TRX2.MOSI
TRX2_RX/TX: MCU_SF.47 (VLCAP2/RP9/RB1)
TRX2_TX/RX: MCU_SF.48 (VLCAP1/RP8/CTED13/INT0/RB0)
V+: OPAMP.8 (V+)
V-: OPAMP.4 (V-)

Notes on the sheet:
APRSDP MCU
OSCILLATOR
APRSDP POWER
TRX1 TX/RX SELECT
PIN HEADER
TRX1 TXD
TRX1 RXD
TRX1 (BIM1H)
VOLTAGE DIVIDER
REMOVABLE LED
TRX2 (AX5243)
TXCO
RF SWITCHES
FLASH MEMORY
SF-WARD 3.3V POWER
PULL UPS
REMOVABLE LEDS
3V3 SUPPLY
SF-WARD MISSION
APRS-DP MISSION
50 PIN CONNECTOR TO BPB

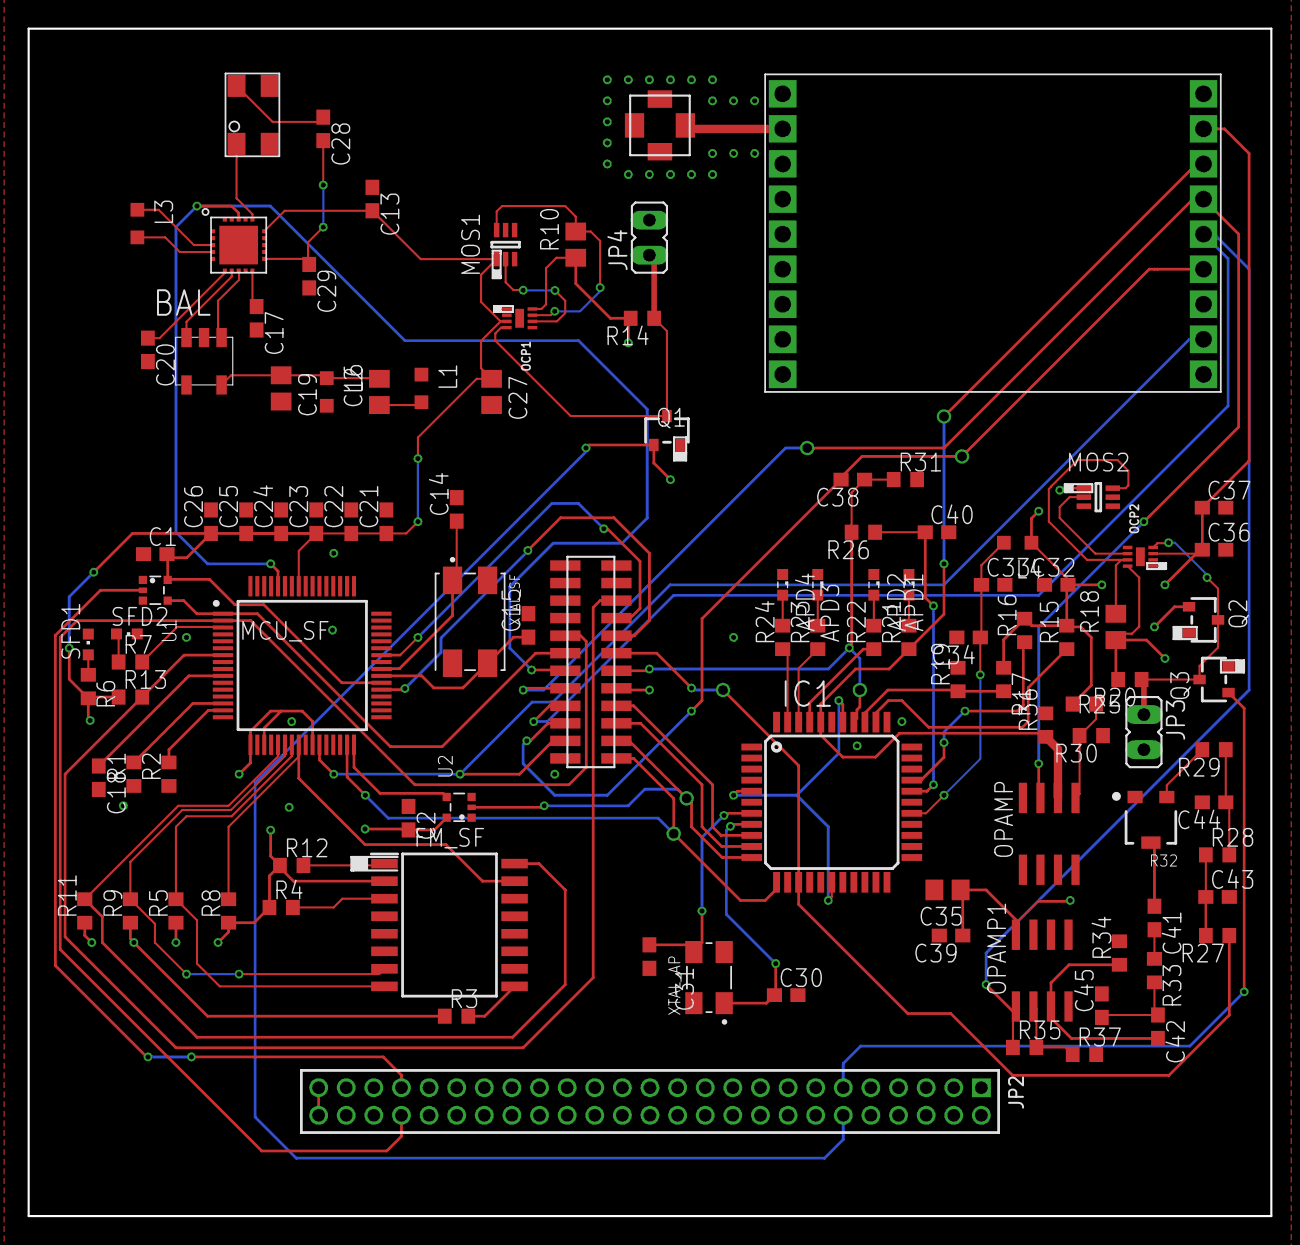
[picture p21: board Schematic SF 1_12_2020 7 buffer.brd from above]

Board: 4 copper layers, 90.0 x 86.0 mm, 107 parts (0 on the bottom side), 84 nets.

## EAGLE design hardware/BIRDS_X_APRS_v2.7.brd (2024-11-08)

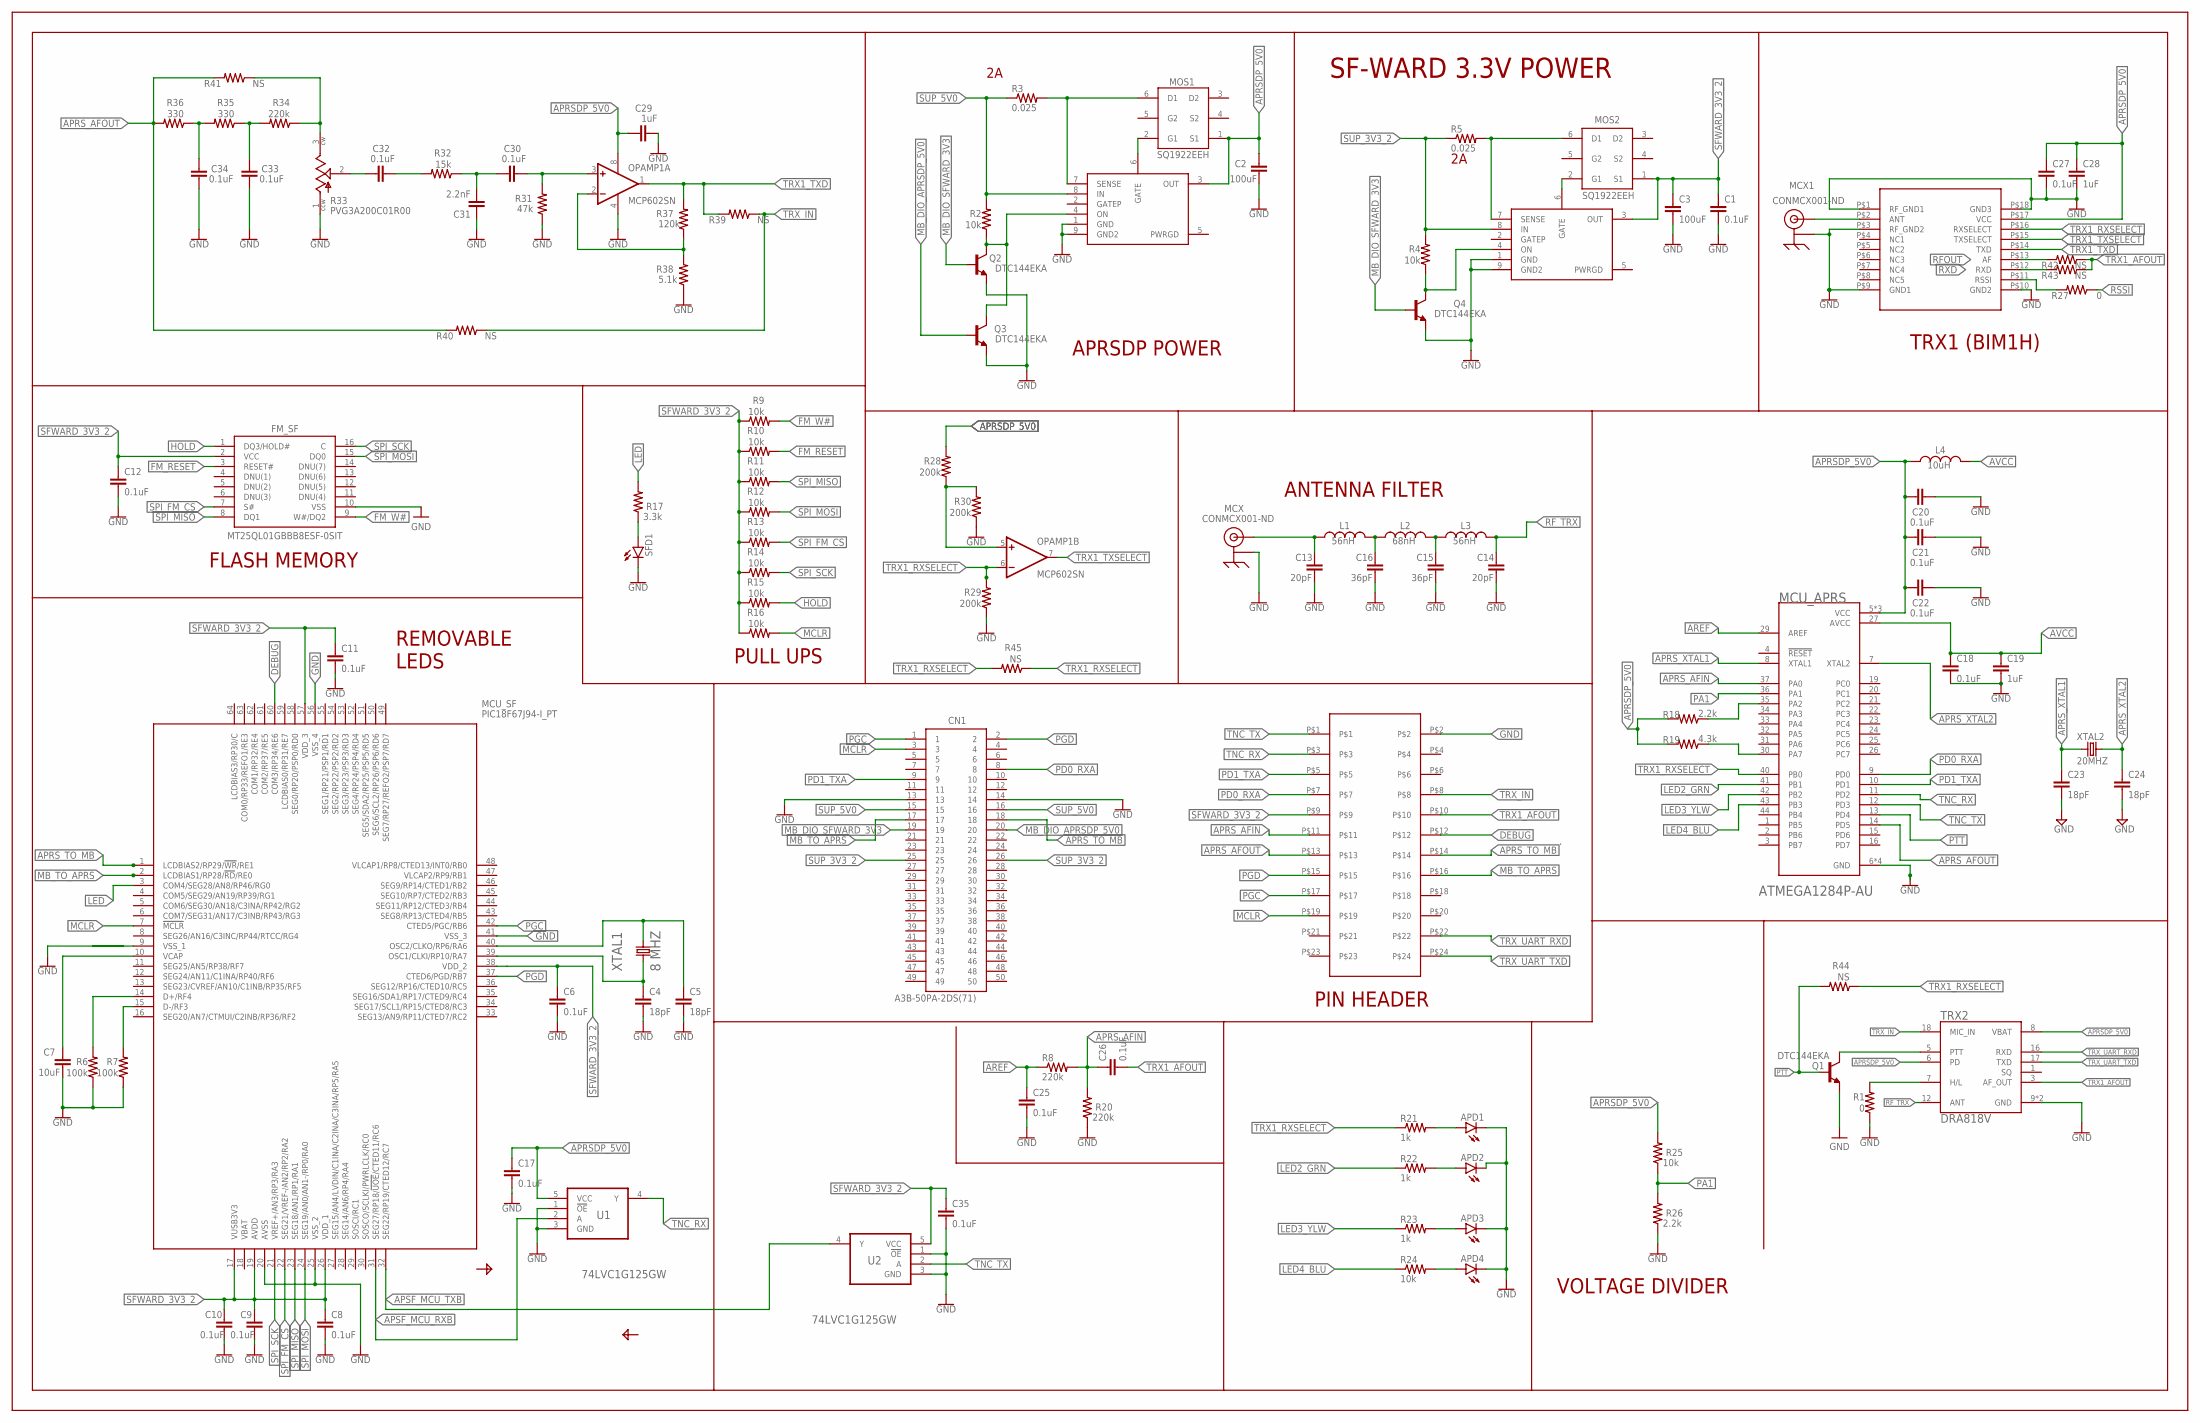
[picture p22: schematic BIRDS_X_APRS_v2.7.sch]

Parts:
APD1, APD2, APD3, APD4: LEDSML0603; SML0603
C1, C6, C8, C9, C10, C11, C12, C17, C18, C20, C21, C22, C25, C26, C27, C30, C32, C33, C34, C35: 0.1uF; M(1005)_US(0402)
C2, C3: 100uF; M(2012)_US(0805)
C4, C5, C23, C24: 18pF; M(1005)_US(0402)
C7: 10uF; M(1608)_US(0603)
C13, C14: 20pF; M(1608)_US(0603)
C15, C16: 36pF; M(1608)_US(0603)
C19, C28, C29: 1uF; M(1005)_US(0402)
C31: 2.2nF; M(1005)_US(0402)
CN1: A3B-50PA-2DS(71)
FM_SF: MT25QL01GBBB8ESF-0SIT; SOIC127P1032X265-16N
JP1: RAB_ACCESS
L1, L3: 56nH; M(2012)_US(0805)
L2: 68nH; M(2012)_US(0805)
L4: 10uH; M(2012)_US(0805)
MCU_APRS: ATMEGA1284P-AU; QFP80P1200X1200X120-44N
MCU_SF: PIC18F67J94-I_PT; QFP50P1200X1200X120-64N
MCX, MCX1: CONMCX001-ND
MOS1, MOS2: SQ1922EEH; SOT65P210X110-6N
OCP1, OCP2: BIRDS5_LTC4361
OPAMP1: MCP602SN; SO08
Q1, Q2, Q3, Q4: DTC144EKA; SOT346-R
R1: 0; M(1005)_US(0402)
R2, R4, R9, R10, R11, R12, R13, R14, R15, R16: 10k; M(1005)_US(0402)
R3, R5: 0.025; M(2012)_US(0805)
R6, R7: 100k; M(1005)_US(0402)
R8, R20, R34: 220k; M(1608)_US(0603)
R17: 3.3k; M(1608)_US(0603)
R18: 2.2k; M(1005)_US(0402)
R19: 4.3k; M(1005)_US(0402)
R21, R22, R23: 1k; M(1608)_US(0603)
R24, R25: 10k; M(1608)_US(0603)
R26: 2.2k; M(1608)_US(0603)
R27: 0; M(1608)_US(0603)
R28, R29, R30: 200k; M(1005)_US(0402)
R31: 47k; M(1608)_US(0603)
R32: 15k; M(1608)_US(0603)
R33: PVG3A200C01R00; TRIM_PVG3A200C01R00
R35, R36: 330; M(1608)_US(0603)
R37: 120k; M(1608)_US(0603)
R38: 5.1k; M(1608)_US(0603)
R39, R40, R41, R42, R43, R44, R45: NS; M(1608)_US(0603)
SFD1: LEDCHIPLED_0603; CHIPLED_0603
TRX1: BIM1H
TRX2: DRA818V; DORJI_DRA818V
U1, U2: 74LVC1G125GW; SOT65P210X110-5N
XTAL1: 8 MHZ; CRYSTAL_SM49
XTAL2: 20MHZ; SM49

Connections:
APRSDP_5V0: C2.1, C17.1, C20.1, C21.1, C22.1, C27.1, C28.1, C29.1, L4.1, MCU_APRS.5 (VCC), MCU_APRS.17 (VCC), MCU_APRS.38 (VCC), MOS1.1 (S1), OCP1.3 (OUT), OPAMP1.8 (V+), R18.2, R19.2, R25.2, R28.2, TRX1.P$17 (VCC), TRX2.6 (PD), TRX2.8 (VBAT), U1.5 (VCC)
APRS_AFIN: C26.1, JP1.P$11, MCU_APRS.37 (PA0), R8.2, R20.2
APRS_AFOUT: JP1.P$13, MCU_APRS.14 (PD5), R36.2, R40.2, R41.2
APRS_TO_MB: CN1.18, JP1.P$14, MCU_SF.1 (LCDBIAS2/RP29/!WR!/RE1)
APRS_XTAL1: C23.1, MCU_APRS.8 (XTAL1), XTAL2.1
APRS_XTAL2: C24.1, MCU_APRS.7 (XTAL2), XTAL2.2
APSF_MCU_RXB: MCU_SF.31 (SEG27/RP18/!UOE!/CTED11/RC6), U1.2 (A)
APSF_MCU_TXB: MCU_SF.32 (SEG22/RP19/CTED12/RC7), U2.4 (Y)
AREF: C25.1, MCU_APRS.29 (AREF), R8.1
AVCC: C18.1, C19.1, L4.2, MCU_APRS.27 (AVCC)
DEBUG: JP1.P$12, MCU_SF.60 (COM3/RP34/RE6)
FM_RESET: FM_SF.3 (RESET#), R10.2
FM_W#: FM_SF.9 (W#/DQ2), R9.2
GATE3: MOS2.2 (G1), OCP2.6 (GATE)
GND: APD1.C, APD2.C, APD3.C, APD4.C, C1.2, C2.2, C3.2, C4.2, C5.2, C6.2, C7.2, C8.2, C9.2, C10.2, C11.2, C12.2, C13.2, C14.2, C15.2, C16.2, C17.2, C18.2, C19.2, C20.2, C21.2, C22.2, C23.2, C24.2, C25.2, C27.2, C28.2, C29.2, C31.1, C33.2, C34.2, C35.2, CN1.13, CN1.14, FM_SF.10 (VSS), JP1.P$2, MCU_APRS.6 (GND), MCU_APRS.18 (GND), MCU_APRS.28 (GND), MCU_APRS.39 (GND), MCU_SF.9 (VSS_1), MCU_SF.20 (AVSS), MCU_SF.25 (VSS_2), MCU_SF.41 (VSS_3), MCU_SF.56 (VSS_4), MCX.2, MCX.3 (2), MCX.4 (2), MCX.5 (2), MCX1.2, MCX1.3 (2), MCX1.4 (2), MCX1.5 (2), OCP1.1 (GND), OCP1.9 (GND2), OCP2.1 (GND), OCP2.9 (GND2), OPAMP1.4 (V-), Q1.1 (E), Q2.1 (E), Q3.1 (E), Q4.1 (E), R1.1, R20.1, R26.1, R30.1, R31.1, R33.1 (CCW), R38.1, TRX1.P$1 (RF_GND1), TRX1.P$3 (RF_GND2), TRX1.P$9 (GND1), TRX1.P$10 (GND2), TRX1.P$18 (GND3), TRX2.9 (GND), TRX2.10 (GND), U1.1 (!OE), U1.3 (GND), U2.1 (!OE), U2.3 (GND)
HOLD: FM_SF.1 (DQ3/HOLD#), R15.2
LED: MCU_SF.3 (COM4/SEG28/AN8/RP46/RG0), R17.2
LED2_GREEN: APD2.A, R22.2
LED2_GRN: MCU_APRS.41 (PB1), R22.1
LED3_YLW: MCU_APRS.42 (PB2), R23.1
LED4_BLU: MCU_APRS.43 (PB3), R24.1
LED4_BLUE: APD4.A, R24.2
LED_3_YELLOW: APD3.A, R23.2
MB_DIO_APRSDP_5V0: CN1.20, Q3.2 (B)
MB_DIO_SFWARD_3V3: CN1.19, Q2.2 (B), Q4.2 (B)
MB_TO_APRS: CN1.17, JP1.P$16, MCU_SF.2 (LCDBIAS1/RP28/!RD!/RE0)
MCLR: CN1.3, JP1.P$19, MCU_SF.7 (!MCLR), R16.2
unnamed: MOS1.2 (G1), OCP1.6 (GATE)
unnamed: C7.1, MCU_SF.10 (VCAP)
unnamed: C5.1, MCU_SF.40 (OSC2/CLKO/RP6/RA6), XTAL1.2
unnamed: MCU_SF.15 (D-/RF3), R7.2
unnamed: MCU_SF.14 (D+/RF4), R6.2
unnamed: R17.1, SFD1.A
unnamed: C15.1, L2.2, L3.1
unnamed: C16.1, L1.2, L2.1
unnamed: C13.1, L1.1, MCX.1
unnamed: R1.2, TRX2.7 (H/L)
unnamed: MCU_APRS.35 (PA2), R18.1
unnamed: MCU_APRS.30 (PA7), R19.1
unnamed: R27.2, TRX1.P$11 (RSSI)
unnamed: MCX1.1, TRX1.P$2 (ANT)
unnamed: OPAMP1.5 (+IN), R28.1, R30.2
unnamed: C32.2, R32.2
unnamed: C30.1, C31.2, R32.1
unnamed: C30.2, OPAMP1.3 (+IN), R31.2
unnamed: Q1.3 (C), TRX2.5 (PTT)
unnamed: C32.1, R33.2 (WIPER)
unnamed: R33.3 (CW), R34.1, R41.1
unnamed: C34.1, R35.2, R36.1
unnamed: C33.1, R34.2, R35.1
unnamed: OPAMP1.2 (-IN), R37.1, R38.2
ON3: OCP2.4 (ON), Q4.3 (C), R4.1
ON4: OCP1.4 (ON), Q2.3 (C), Q3.3 (C), R2.1
OSC2: C4.1, MCU_SF.39 (OSC1/CLKI/RP10/RA7), XTAL1.1
PA1: MCU_APRS.36 (PA1), R25.1, R26.2
PD0_RXA: CN1.8, JP1.P$7, MCU_APRS.9 (PD0)
PD1_TXA: CN1.9, JP1.P$5, MCU_APRS.10 (PD1)
PGC: CN1.1, JP1.P$17, MCU_SF.42 (CTED5/PGC/RB6)
PGD: CN1.2, JP1.P$15, MCU_SF.37 (CTED6/PGD/RB7)
PTT: MCU_APRS.13 (PD4), Q1.2 (B), R44.2
RFOUT: R42.2, TRX1.P$13 (AF)
RF_TRX: C14.1, L3.2, TRX2.12 (ANT)
RSSI: R27.1
RXD: R43.2, TRX1.P$12 (RXD)
SENSE3: MOS2.6 (D1), OCP2.7 (SENSE), R5.2
SENSE4: MOS1.6 (D1), OCP1.7 (SENSE), R3.2
SFWARD_3V3_2: C1.1, C3.1, C6.1, C8.1, C9.1, C10.1, C11.1, C12.1, C35.1, FM_SF.2 (VCC), JP1.P$9, MCU_SF.17 (VUSB3V3), MCU_SF.19 (AVDD), MCU_SF.26 (VDD_1), MCU_SF.38 (VDD_2), MCU_SF.57 (VDD_3), MOS2.1 (S1), OCP2.3 (OUT), R9.1, R10.1, R11.1, R12.1, R13.1, R14.1, R15.1, R16.1, U2.5 (VCC)
SPI_FM_CS: FM_SF.7 (S#), MCU_SF.22 (SEG21/VREF-/AN2/RP2/RA2), R13.2
SPI_MISO: FM_SF.8 (DQ1), MCU_SF.23 (SEG18/AN1/RP1/RA1), R11.2
SPI_MOSI: FM_SF.15 (DQ0), MCU_SF.24 (SEG19/AN0/AN1-/RP0/RA0), R12.2
SPI_SCK: FM_SF.16 (C), MCU_SF.21 (VREF+/AN3/RP3/RA3), R14.2
SUP_3V3_2: CN1.25, CN1.26, OCP2.8 (IN), R4.2, R5.1
SUP_5V0: CN1.15, CN1.16, OCP1.8 (IN), R2.2, R3.1
TNC_RX: JP1.P$3, MCU_APRS.11 (PD2), U1.4 (Y)
TNC_TX: JP1.P$1, MCU_APRS.12 (PD3), U2.2 (A)
TRX1_AFOUT: C26.2, JP1.P$10, R42.1, R43.1, TRX2.3 (AF_OUT)
TRX1_RXSELECT: MCU_APRS.40 (PB0), OPAMP1.6 (-IN), R21.1, R29.2, R44.1, R45.1, R45.2, TRX1.P$16 (RXSELECT)
TRX1_RX_LED: APD1.A, R21.2
TRX1_TXD: OPAMP1.1 (OUT), R37.2, R39.2, TRX1.P$14 (TXD)
TRX1_TXSELECT: OPAMP1.7 (OUT), TRX1.P$15 (TXSELECT)
TRX_IN: JP1.P$8, R39.1, R40.1, TRX2.18 (MIC_IN)
TRX_UART_RXD: JP1.P$22, TRX2.16 (RXD)
TRX_UART_TXD: JP1.P$24, TRX2.17 (TXD)

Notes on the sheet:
APRSDP POWER
SF-WARD 3.3V POWER
FLASH MEMORY
PULL UPS
REMOVABLE LEDS
ANTENNA FILTER
PIN HEADER
VOLTAGE DIVIDER
TRX1 (BIM1H)



Board: 4 copper layers, 79.0 x 81.0 mm, 111 parts (4 on the bottom side), 82 nets.

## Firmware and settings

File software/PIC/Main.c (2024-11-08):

//***************************************************************************************
/*
                   

*/
//****************************************************************************************

#include <18F67J94.h>
#fuses NOWDT
#use delay(internal = 16MHz)
#use rs232(baud=9600, parity=N, xmit=PIN_E1,rcv=pin_E0,bits=8, stream= mboss,force_sw)
char UF = 0xCC;
unsigned int32 NEXT_B_ADD_DP = 0x00020000;
unsigned int32 NEXT_B_ADD_SF = 0x00030000;

#include <pic_settings.c>
#include <Flashmem.c>

char uartflag = 0;
#include <APRS Settings.c>
#include <Mode_Selection.c>



//********************************* Basic Setting ********************************
//
//********************************************************************************
char C_6;

void Setting()
{
   C_6 = input(PIN_C6);
   
   enable_interrupts(int_rda);
   enable_interrupts(int_rda2);
   enable_interrupts(GLOBAL);
   //delay_ms(3000);
   
   //TRYING_TO_PUT_DIGIPETER_TO_MONITOR_MODE(2);
   //boot_Kiss_Mode(1000);
   // TNC_Settings(2000)
   
   if( BYTE_READ(0x000AFFFF) != 0xFF ) SECTOR_ERASE(SNF_LOCATION,64);
   if( BYTE_READ(0x000BFFFF) != 0xFF ) SECTOR_ERASE(DGP_LOCATION,64);
}



void main()
{
   //delay_ms(2000);
   Setting();
   fprintf(debug, "PIC Booting \n\r"); 
   
   while(true)
   {  
      CHECK_UART_INCOMING_FROM_MBOSS();          // Function wrote in PIC Seeting.c 
      TNC_MANUAL_SETTINGS_COMMAND();             // Function wrote in PIC Seeting.c
      
      if( UF == 0xCC ) CHECK_KISS_FRAME_DATA_AND_SAVE(50000);
      
      if( UF == 0xDD )
      {
         while( UART1_Available() )
         {
            fputc(UART1_Read(), debug );
         }
      }
      
      if( (MBOSS_TO_APRS_ARRAY[0]==0xE0) && (MBOSS_TO_APRS_ARRAY[8]==0xED) ) // Frame Identification 
      {  
         //___________________________________________________________
         fprintf(debug, "CMD from Mission BOSS --> "); 
         for(int i = 0; i<9; i++)
         {
            fprintf(debug,"%X ", MBOSS_TO_APRS_ARRAY[i]);
         }
         fprintf(debug, "\n\r" );
         //___________________________________________________________
           
         Digipeter_ON()             ;                     // 0x
         Digipeter_OFF()            ;                     // 0x
         STORE_AND_FORWARD_ON()     ;                     // 0x
         DATA_TRANSFER_IN_DP_MODE() ;                     // 0x
         DATA_TRANSFER_IN_SNF_MODE();                     // 0x
         DATA_SECTORS_ERASE()       ;                     // 0x  //
         Beacon_ON()                ;                     // 0x
         Beacon_OFF()               ;                     // 0x//
         
         CLEAR_DATA_ARRAY(MBOSS_TO_APRS_ARRAY, 50); 
      }      
   }
}

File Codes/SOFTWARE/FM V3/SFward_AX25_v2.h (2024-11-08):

#include <stdint.h>
#include <ctype.h> 
#include <stdio.h>
 
 
//Start of ACS
#define LED_INDICATOR_PIN PIN_G0       //Pin used as indicator for testing
//#define TXONGOING_PIN PIN_B3           //Pin used to indicate that TNC module is still transmitting audio to BIM1H
//#define APSF_FM4_CS PIN_A3             //Chip Select 1, 0 means that S&F flash memory is selected, 1 means deselected

#define SOFTUART_RXPIN PIN_C7          //PIC16F1788 pin #18
#define SOFTUART_TXPIN PIN_C6          //PIC16F1788 pin #17

//#define APSF_FLAG PIN_A5   //pin used by APSF MCU to inform COM96 MCU that it has saved an uplink command received from BIRDS GS

#define UART_BAUDRATE 19.2      //in kbps
#define UART_BITPERIOD 52        //in us
#define UART_HALFBITPERIOD 26    //in us
#define UART_STOPBITPERIOD 52    //in us

#define INFO_FIELD_LEN  155       //number of bytes of AX.25 Information field
//#define UART_RXDATA_MAXLEN (2+16+INFO_FIELD_LEN+1+20)    //number of bytes of AX.25 frame including 2-byte KISS start, 6 bytes dest CS, 1 byte dest SSID, 6 bytes source CS, 1 byte source SSID, 1 byte control field, 1 byte PID, info field, 1-byte KISS end, 20-byte margin
//#define UART_TXDATA_MAXLEN (2+16+INFO_FIELD_LEN+1+20)    //number of bytes of AX.25 frame including 2-byte KISS start, 6 bytes dest CS, 1 byte dest SSID, 6 bytes source CS, 1 byte source SSID, 1 byte control field, 1 byte PID, info field, 1-byte KISS end, 20-byte margin   
#define UART_RXDATA_MAXLEN 512
#define UART_TXDATA_MAXLEN 128


#define TX_DEST_CALLSIGN   ((unsigned char*)"S&FGST")    //destination callsign for downlink
#define TX_SOURCE_CALLSIGN ((unsigned char*)"JG6YKM")    //source callsign for downlink
#define RX_DEST_CALLSIGN   ((unsigned char*)"JG6YKM")    //destination callsign for uplink
#define RX_SOURCE_CALLSIGN ((unsigned char*)"S&FGST")    //source callsign for uplink
#define RECEIVEPACKET_END  ';'  //End of transmission block

#define TNC_PROCDELAY   100   //in ms

#define FEND   (unsigned char)0xC0  //192
#define FESC   (unsigned char)0xDB  //219
#define TFEND  (unsigned char)0xDC  //220
#define TFESC  (unsigned char)0xDD  //221

//function prototypes
unsigned int16 KISSframe_to_AX25packet(unsigned char* KISSframe, unsigned int16 KISSframe_len, unsigned char* AX25packet);
unsigned int16 AX25packet_to_KISSframe(unsigned char* AX25packet, unsigned int16 AX25packet_len, unsigned char* KISSframe);
int8 parse_received_packet();
void send_acknowledgment_packet();
void send_acknowledgment_packet_forcommanduplink();
void send_TLE_packet();
void save_TLE();
void save_received_frame();


void softwareUART_init();
unsigned int16 receive_UARTdata(unsigned char* received_data);
unsigned int16 transmit_UARTdata(unsigned char* transmit_data, unsigned int16 transmit_data_len);
unsigned char softwareUART_receive_byte();



//Global variables
unsigned int8 TX_KISSframe_len = 0;    //number of bytes of received KISS frame
unsigned char TX_KISSframe[UART_TXDATA_MAXLEN] = {};
unsigned int8 TX_packet_len = 0;      //number of bytes of downlink command data to be transmitted, including dest/source CSs and SSIDs, control, PID, info fields, 2-byte FCS and RECEIVEPACKET_END, but excludiing end/start flags and bit stuffs
unsigned char TX_packet[UART_TXDATA_MAXLEN] = {};
//unsigned char TX_callsign_dest[6];
unsigned char TX_SSID_dest = 0x30;
//unsigned char TX_callsign_source[6];                              
unsigned char TX_SSID_source = 0x30;           
unsigned char TX_control = 0x3E;                                
unsigned char TX_PID = 0xF0; 


int16 RX_KISSframe_len = 0;    //number of bytes of received KISS frame
//unsigned int8 RX_KISSframe[UART_RXDATA_MAXLEN] = {};
//RX_KISSframe={0xC0, 0x00, 0x82, 0xA0 , 0x96 , 0x60 , 0x60 , 0x66 , 0x60 , 0x94 , 0x8E , 0x6C , 0xB2 , 0x84 , 0xAE , 0xEE , 0x82 , 0xA0 , 0xA4 , 0xA6 , 0x82 , 0xA8 , 0x61 , 0x03 , 0xF0 , 0x3A , 0x42 , 0x49 , 0x52 , 0x44 , 0x53 , 0x34 , 0x20 , 0x20 , 0x20 , 0x3A , 0x61 , 0x61 , 0x61 , 0x61 , 0x61 , 0x7B , 0x32 , 0x37 , 0x0D , 0xC0};

unsigned int8 RX_KISSframe[] ={0xC0, 0x00, 0x4A, 0x47 , 0x36 , 0x59 , 0x4B , 0x4D , 0x30 , 0x53 , 0x26 , 0x46 , 0x47 , 0x53 , 0x54 , 0x31 , 0x3E , 0xF0 , 0x53 , 0x46 , 0x00 , 0x00 , 0x51 , 0x31 , 0x38 , 0x30 , 0x37 , 0x30 , 0x31 , 0x33 , 0x31 , 0x35 , 0x30 , 0x35 , 0x31 , 0x38 , 0x55 , 0x37 , 0x31 , 0x30 , 0x31 , 0x33 , 0x31 , 0x35 , 0x32 , 0x30 , 0x32 , 0x32 , 0x35 , 0x53 , 0xC0};


unsigned int16 RX_packet_len = 0;    //number of bytes of uplink command data received including dest/source CSs and SSIDs, control, PID, info fields and 2-byte FCS, but excluding RECEIVEPACKET_END, end/start flags and bit stuffs
unsigned char RX_packet[UART_RXDATA_MAXLEN] = {};

unsigned char RX_callsign_dest[7] = {'\0','\0','\0','\0','\0','\0','\0'};
unsigned char RX_SSID_dest = 0x30;
unsigned char RX_callsign_source[7] = {'\0','\0','\0','\0','\0','\0','\0'};                                 
unsigned char RX_SSID_source = 0x30;           
unsigned char RX_control = 0x3E;                                
unsigned char RX_PID = 0xF0; 
unsigned char RX_info_field[256];
//unsigned char RX_FCS[2];
                
unsigned char info_header[2] = {'S', 'F'};                      
unsigned char info_footer[2] = {'S', 'F'};                        
                      
 
//Convert only one KISS frame to an AX.25 packet

unsigned int16 KISSframe_to_AX25packet(unsigned char* KISSframe, unsigned int16 KISSframe_len, unsigned char* AX25packet)
{
   unsigned int16 RX_AX25packet_len = 0;   //number of recently decoded bytes and serves as index to where the next decoded byte should be placed
   
   //Check if valid KISS frame
   if(!(RX_KISSframe[0]==FEND && RX_KISSframe[RX_KISSframe_len-1]==FEND)) return RX_AX25packet_len;
   
   //Else, assume a valid KISS frame, begin decoding at the third byte and stop before the end of frame
   for(unsigned int16 k=2; k < (RX_KISSframe_len-1); k++)
   {
      //Corresponding to received AX.25 data FEND
      if(RX_KISSframe[k]==TFESC && RX_KISSframe[k-1]==FESC) RX_packet[RX_AX25packet_len++]=FESC; 
      
      //Corresponding to received AX.25 data FESC
      else if(RX_KISSframe[k]==TFESC && RX_KISSframe[k-1]==FESC) RX_packet[RX_AX25packet_len++]=FESC;
      
      //Special ESC character was encountered in the last iteration but present byte is invalid
      else if(RX_KISSframe[k-1]==FESC && !(RX_KISSframe[k]==TFEND || RX_KISSframe[k]==TFESC))
      {
         RX_AX25packet_len = 0;
         break;
      }

      //Special ESC character encountered so examine the next byte
      else if (RX_KISSframe[k]==FESC) continue;    //Escape mode
      
      //No special character, just copy the received data as it is
      else RX_packet[RX_AX25packet_len++]=RX_KISSframe[k];
   
   }
   return RX_AX25packet_len;
}
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

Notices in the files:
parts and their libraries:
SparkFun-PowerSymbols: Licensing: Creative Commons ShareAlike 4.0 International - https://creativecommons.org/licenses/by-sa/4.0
